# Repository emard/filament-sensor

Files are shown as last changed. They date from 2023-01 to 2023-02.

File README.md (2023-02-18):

# Filament Sensor

Sensor detects presence or absence of the filament.
Openscad 3D Printable models for filament sensors
with cotactless Hall sensor or with mechanical microswitch.

# Hall sensor

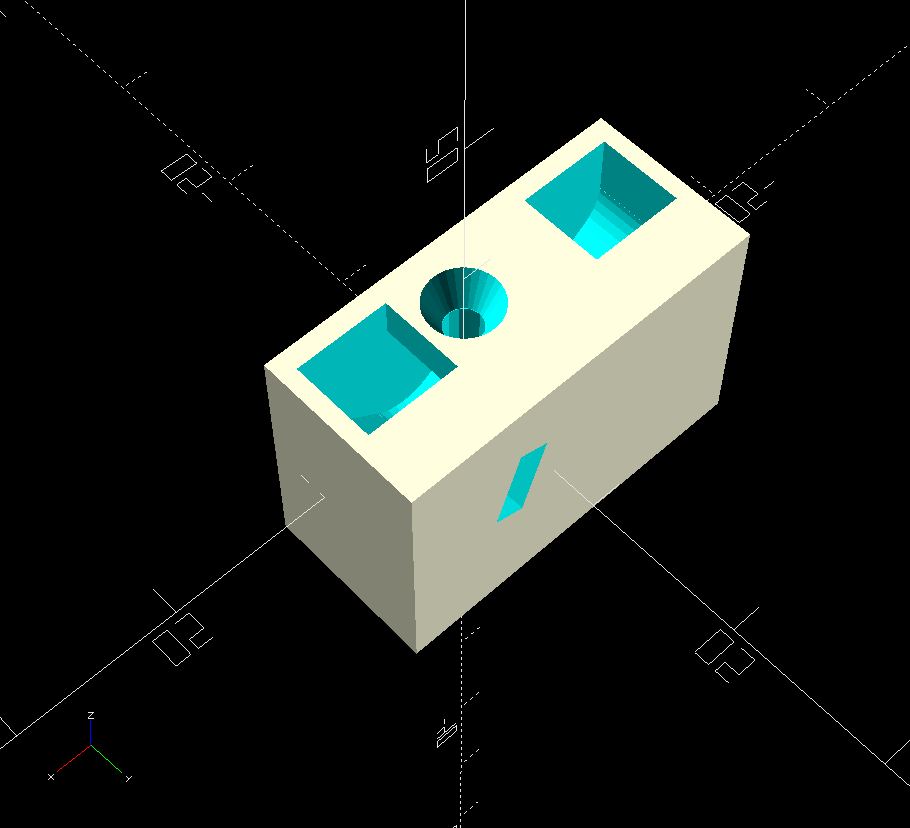
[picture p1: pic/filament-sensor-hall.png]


Applies very small force to the filament,
minimizing friction.

    prusa has this logic in its original IR filament sensor
    sensor OUT:
    0 (LOW)  LOADED
    1 (HIGH) EMPTY
    IR sensor pinout
    +  +5V
    O  OUT
    -  GND
    
    MK2S rambo13a 10-pin connector looking at PCB pins
    ---------
    x x x x x
    x s x - +
    ---------
    -=GND, +=+5V, s=signal
    
    MK3 einsy10a 10-pin connector looking at PCB pins
    ---   ---
    x x x x x
    s x x - +
    ---------
    -=GND, +=+5V, s=signal
    
    HALL sensor Honeywell SS411P or SS495A
    on package is written 411P or 95A
    pinout looking at pins, plastic case at the back
      _______
     / + - o \
     ---------
    
    connect
     - -
     + +
     s o
    
    Prusa MK2.5S firmware can be loaded to MK2S
    Support -> Sensor info
    Fil. sensor: 1-LOADED, 0-EMPTY

Magnet (5x5 mm Neodymium cylinder) is the only moving
part. Solid state Hall sensor (Honeywell SS495A or similar for 5V)
in 3-pin transistor plastic case directly connects to
printer motherboard electronics.

When sensor is empty, magnet is placed at the
position in channel close to the empty filament
guide. Inserted filament displaces the magnet.

Best location for the Hall sensor is where magnetic
flux reverses sign when filament is inserted,
so the sensor reliably reads logical 1 or 0.
To invert logic, flip both magnets or flip the sensor.

Flipping or using different sensor may need adjustment,
experiment with position along the channel, in case of
false runout, reduce the X parameter in steps of 0.1:

    hall_pos = [X,Y,Z];

Hall sensor used is SS411P digital output with bipolar
triggering in range of +50/-50 Gauss or SS495A analog
rail-to-rail output with high sensitivity 3 mV/Gauss = 30 V/Tesla.
AH3377 with unipolar triggering in range of +115/+90
Gauss can be used too but I haven't tried it.

Cut small piece of universal PCB, solder 3-pin connector
on top side, sensor on bottom side. Insulate sensor
middle terminal (-) as it crosses over (o) terminal.
Default sensor orientation is flat side towards filament.

When filament moves thru the guide, it can
either slide over the magnet or rotate the
magnet in the channel. In either case, friction
is very small.

When filament is removed, magnet returns to its
default position by its own weight or by attractive
force from the second magnet.

Second magnet should be used if filament sensor is
not always vertical. It provides a more reliable return
but it increases force, increasing the friction too.
Friction can be tuned by varying distance of
second magnet from the filament detection magnet.

Attractive force holds magnets together so they
won't leave sensor easily. To remove inserted
DxH=5x5 mm magnets, insert filament, try to shake
it out, touch it with some steel or approach
external magnet DxH=10x5 mm from the side and
drag it.

# Mechanical switch

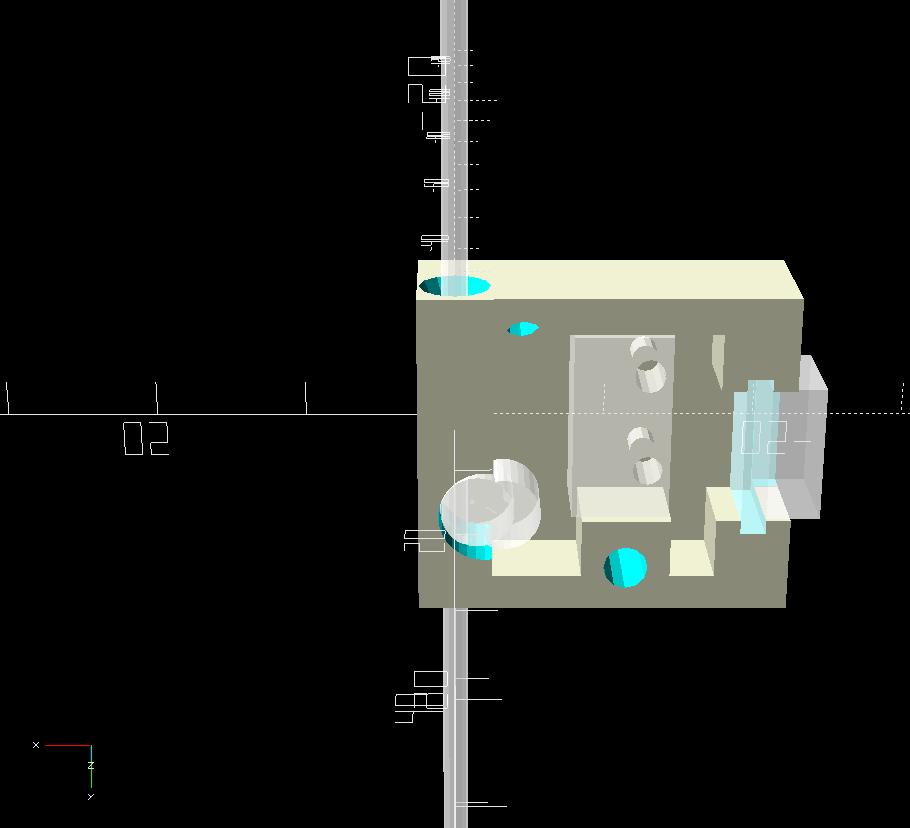
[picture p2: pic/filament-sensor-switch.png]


Applies more friction to the filament than
the Hall sensor.

Mechanical switch with roller applies its designed
force to the filament. Roller should be precisely
positioned relative to the filament to reliably
trigger so there is not much space to tune the
force.

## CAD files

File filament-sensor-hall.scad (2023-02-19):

// filament sensor with magnet and HALL sensor

// prusa has this logic in its original IR filament sensor
// sensor OUT:
// 0 (LOW)  LOADED
// 1 (HIGH) EMPTY
// IR sensor pinout
// +  +5V
// O  OUT
// -  GND

// MK2S rambo13a 10-pin connector looking at PCB pins
// ---------
// x x x x x
// x s x - +
// ---------
//    P3
// -=GND, +=+5V, s=signal

// MK3 einsy10a 10-pin connector looking at PCB pins
// ---   ---
// x x x x x
// s x x - +
// ---------
// -=GND, +=+5V, s=signal

// HALL sensor Honeywell SS495A, on package is written 95A
// pinout looking at pins, plastic case at the back
//   _______
//  / + - o \
//  ---------

// connect
//  - -
//  + +
//  s o

// Prusa MK2.5S firmware can be loaded to MK2S
// Support -> Sensor info
// Fil. sensor: 1-LOADED, 0-EMPTY

hall_pos = [0.0,0,6]; // in case of false filament runout, decrease X in steps of 0.1

hall_sensor_dim = [5,5,1.8];
//hall_sensor_dim = [4.06, 3.0, 1.6]; // Honeywell SS495A package, with enlarge factor for hole
filament_hole_d = 2.3; // 1.75mm should freely passthru

// the filament sensor cube dim
guide_dim=[25,16,8+3]; // reduce Z to see cross-section
guide_pos=[-2.5,0,1.5];

magnet2_pos = [-5,0,0]; // adjust X to tune force

connector_pcb_cube=[1.7,13,7.7];
connector_pcb_pos=[-12,0,9];


mounting_holes=[[-3,-5],[6,5],[-6,5]];

module hall_sensor()
{
  cube(hall_sensor_dim, center=true);
}

module magnet()
{
  cylinder(d=magnet_dim[0], h=magnet_dim[1], $fn=24, center=true);
}


module filament()
{
  translate([0,0,0])
    rotate([90,0,0])
    cylinder(d=1.75,h=70,$fn=12,center=true);
}

module roller_cutter(have_sensor=1)
{
  roller_pos = [2.0,-1,0];
  roller_dim = [6.0,5.4]; // DxH
  channel_angle = 38; // fall down angle
  channel_dim = [5,roller_dim[0],roller_dim[1]]; // from center of roller, at fall down angle
  top_insert_dim = [10,roller_dim[0]+0,roller_dim[1]];
  // roller cut
  translate(roller_pos)
  cylinder(d=roller_dim[0],h=roller_dim[1],$fn=32,center=true);
  // angular
  translate(roller_pos)
  rotate([0,0,-channel_angle])
  {
    // channel
    translate([channel_dim[0]/2,0,0])
    cube(channel_dim,center=true);
    // circular knee transition to upwards channel
    translate([channel_dim[0],0,0])
      cylinder(d=top_insert_dim[1],h=roller_dim[1],$fn=32,center=true);
    // cut upwards channel to insert magnet
    translate([channel_dim[0],0,0])
    rotate([0,0,-90+channel_angle])
    translate([top_insert_dim[0]/2,0,0])
    cube(top_insert_dim,center=true);
    // cut for sensor
    if(have_sensor>0.5)
    translate(hall_pos)
      //rotate([0,0,channel_angle])
      rotate([90,0,90+channel_angle/4])
      cube(hall_sensor_dim,center=true);
  }
}


module filament_guide()
{
  difference()
  {
    union()
    {
      // guide block
      translate(guide_pos)
        cube(guide_dim,center=true);
    }
    // main roller hole and sensor
    roller_cutter();
    // additional magnet to increase force
    translate(magnet2_pos) // more X distance less force
      scale([-1,1,1]) // mirror
        roller_cutter(have_sensor=0);
    // filament hole thru all
    rotate([90,0,0])
    {
      cylinder(d=filament_hole_d,h=50,$fn=12,center=true);
      // overhang fix
      if(0)
      translate([0.4,0,0])
        cylinder(d=filament_hole_d*0.8,h=50,$fn=12,center=true);
      // conical lead-in
      translate([0,0,-guide_pos[1]+2+guide_dim[1]/2-11+8])
        cylinder(d1=filament_hole_d,d2=filament_hole_d*2,h=2.1,$fn=30,center=true);
      // conical lead-out
      if(1)
      translate([0,0,-guide_pos[1]+2-guide_dim[1]/2+11-12])
        cylinder(d2=filament_hole_d,d1=filament_hole_d*2.08,h=2.1,$fn=30,center=true);
    }
  }
}

module holder_bars()
{
  // filament entry side
  holder_pos = guide_pos + [0,0,9];
  holder_dim = guide_dim - [0,0,4];
  holder_thick = 2;
  holder_backplate_thick = 1;
  translate(holder_pos)
    difference()
    {
      cube(holder_dim,center=true);
      translate([0,0,-holder_backplate_thick/2-0.01])
      cube(holder_dim+[-holder_thick*2,-holder_thick*3,-holder_backplate_thick],center=true);
    }
}

module baseplate()
{
    translate([10,2,-1.5-6/2])
      cube([25,22,3],center=true);
}

module screw_holes(d=3, h=30)
{
  // mounting holes
  for(i=[0,1,2])
      translate(mounting_holes[i])
        rotate([0,0,90])
          cylinder(d=d,h=h,$fn=12,center=true);
}

module connector_pcb()
{
  translate(connector_pcb_pos)
  cube(connector_pcb_cube,center=true);
  // connector front cut
  translate(connector_pcb_pos+[-2,0,0])
    cube([5,10,7],center=true);
}

// mounting spacer with connector cut and screw holes
module spacer()
{
   difference()
   {
     union()
     {
       holder_bars();
       translate([0,0,10.5])
       screw_holes(d=4,h=7);
     }
     screw_holes(d=1.8);
     translate([0,0,0.2])
     connector_pcb();
   }
}

cableorg_holes_pos = [[0,32], [0,22]];
module cableorg_holes(d=1.8)
{
    // holes for cable organizer
    for(i=[0,1])
    translate(cableorg_holes_pos[i])
      rotate([0,0,0])
        cylinder(d=d,h=20,$fn=12,center=true);
}

module magnets_cover()
{
  standoff = 0.3; // tolerance standoff
  // covers 1st magnet
  translate([-6,-9-standoff,7])
    cube([7,2,7+11],center=true);
  // sovers 2nd magnet
  translate([11,-9-standoff,7])
    cube([7,2,7+11],center=true);
  // connects holders together
  if(0)
  translate([4,-9-standoff,3])
    cube([20,2,10],center=true);
  // standoff "glue"
  translate([2.5,-8-standoff/2,1.5])
    cube([25,standoff,7],center=true);
}

module pendulum()
{
  // for M8 rod
  pendulum_dim = [7,40,7];
  pendulum_pos = [0,28,1.5];
  ring_inner_d =  9;
  ring_outer_d = 15;

  // for printed holder old design
  /*
  pendulum_dim = [7,40,5];
  pendulum_pos = [0,28,0.5];
  ring_inner_d = 10;
  ring_outer_d = 15;
  */

  difference()
  {
    union()
    {
      translate(pendulum_pos)
        cube(pendulum_dim, center=true);
      translate(pendulum_pos+[0,pendulum_dim[1]/2,0])
        cylinder(d=ring_outer_d,h=pendulum_dim[2],$fn=32,center=true);
    }
    // hole for bearing
    translate(pendulum_pos+[0,pendulum_dim[1]/2,0])
        cylinder(d=ring_inner_d,h=pendulum_dim[2]+1,$fn=32,center=true);
    cableorg_holes();
  }
  magnets_cover();
}

module cable_cover()
{
  difference()
  {
    translate([0,27,5])
    cube([7,15,3],center=true);
    translate([0,27,4])
    cube([8,6,1.01],center=true);
    cableorg_holes(d=3);
  }
}

module pendulum_holder_screw_holes()
{
  mounting_holes=[[10,10,0],[-10,-10,0]];
     // mounting holes
  for(i=[0,1])
      translate(mounting_holes[i])
        rotate([0,0,90])
        {
          cylinder(d=1.8,h=20,$fn=12,center=true);
          // hole for sunken head
          if(0)
          translate([0,0,5])
          cylinder(d=6,h=10,$fn=12,center=true);
        }
}

module pendulum_holder()
{
  plate_box = [25,30,4];
  axis_pos = [0,-3,0];
  axis = [8,6]; // d,h
  difference()
  {
    cube(plate_box,center=true);
    pendulum_holder_screw_holes();
  }
  // axis
  translate(axis_pos+[0,0,plate_box[2]/2+axis[1]/2])
  difference()
  {
    cylinder(d=axis[0],h=axis[1],$fn=32,center=true);
    // screw hole
    cylinder(d=1.8,h=axis[1]+1,$fn=32,center=true);
  }
  // filament holder
  if(1)
  translate([0,12,7])
    cube([5,6,10],center=true);
  // circular holder
  translate([0,12,30])
    rotate([90,90,0])
    difference()
    {
      cylinder(d=40,h=6,$fn=6,center=true);
      cylinder(d=30,h=11,$fn=6,center=true);
    }
}

module holder_disc()
{
  difference()
  {
    cylinder(d=15,h=2,$fn=32,center=true);
    cylinder(d=3,h=3,$fn=32,center=true);
  }
}

module pendulum_assembly()
{
  translate([0,0,12])
  rotate([180,0,180])
  spacer();
  pendulum();  
}

// sensor
module sensor_assembly()
{
rotate([-90,0,0])
{
%filament();
%connector_pcb();
difference()
{
  union()
  {
    filament_guide();
    //holder_bars();
  }
  connector_pcb();
  screw_holes();
}
translate([0,0,12+1])
rotate([180,0,180])
%pendulum_assembly();
// %spacer();
}
}

if(1)
  sensor_assembly();

// pendulum with backplate
if(0)
{
  pendulum_assembly();
}

// pendulum holder to be screwd on snap-on adapter
if(0)
{
  pendulum_holder();
}

// disc on top of the holder
if(0)
  holder_disc();

// spacer disk for too long screws
if(0)
  difference()
  {
    cylinder(d=6.0,h=1.5,$fn=12,center=true);
    cylinder(d=2.5,h=2.0,$fn=12,center=true);
  }

if(0)
  cable_cover();

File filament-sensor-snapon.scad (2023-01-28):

frame_cube=[40.4,6.4,50];


snapon_points=[
 // bottom part near frame
 [-frame_cube[0]/2,frame_cube[1]/2],[-frame_cube[0]/2,-frame_cube[1]/2],
 // click notch slightly up
 [-frame_cube[0]/2+1,-frame_cube[1]/2],[-frame_cube[0]/2,-frame_cube[1]/2-2],
 // bottom edge
 [-25,-frame_cube[1]/2-2],[-25,9],
 // back side
 [25,9],[25,-9],
 // holder notch
 [15,-9],[15,-frame_cube[1]/2],[frame_cube[0]/2,-frame_cube[1]/2],
 // angled insertion helper
 [frame_cube[0]/2,frame_cube[1]/2+1],[15,frame_cube[1]/2]
 // insertion
];

extbar_thick = 5.5;
angular_adjust = 3;
extbar_points = [
  // go up
  [25,-9], [30,-9],
  // lean forward
  [70,-60], [160, -60],
  // back side return
  [160, -60+extbar_thick], [70+angular_adjust, -60+extbar_thick],
  // return down
  [30+angular_adjust,-9+extbar_thick], [25,-9+extbar_thick]
];

module frame()
{
  cube(frame_cube,center=true);
}

module mounting_holes_cutter()
{
  // [[4.5,-6],[11.5,10]];
  offset=[145,-60,0];
  holes_pos=[[offset[0]+10,offset[1],offset[2]-10],[offset[0]-10,offset[1],offset[2]+10]];
  for(i=[0,1])
    translate(holes_pos[i])
      rotate([90,0,0])
      cylinder(d=3,h=20,$fn=12,center=true);
}

module snapon_clip()
{
  linear_extrude(30,center=true)
  polygon(points=snapon_points);
}

module snapon_clip_with_holes()
{
  difference()
  {
    union()
    {
      snapon_clip();
      extension_bar();
    }
    mounting_holes_cutter();
  }
}

module extension_bar()
{
  linear_extrude(30,center=true)
  polygon(points=extbar_points);
}

%frame();
snapon_clip_with_holes();

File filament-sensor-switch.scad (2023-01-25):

// switch D2F-01L2-D with big roller 5mm dia
// https://omronfs.omron.com/en_US/ecb/products/pdf/en-d2f.pdf

// prusa this logic in its original IR filament sensor
// sensor OUT:
// 0 (LOW)  filament inserted
// 1 (HIGH) filament runout

// MK2S 10-pin connector looking at PCB pins
// ---------
// x x x x x
// - s x - +
// ---------
// -=GND, +=+5V, s=signal

// MK3 10-pin connector looking at PCB pins, notch on top
// ---   ---
// x x x x x
// s x x - +
// ---------
// -=GND, +=+5V, s=signal

// switch pinout, button on top left
//  _-___
// |_____|
//  N O C
//
//  N-O : NO (normally open)
//  N-C : NC (normally closed)

// connect bare switch
// - O
// + C
// s N

adjust_click = 0.2; // to reliably click move +:closer -:away from filament
filament_hole_d = 2.4; // 1.75mm should freely passthru

module switch()
{
  swbox = [6.5,12.7,5.7];
  hole_pos = [[5,3],[5,-3.5],[5,-3.8]];
  hole_dia = 2;
  roller = [5,4]; // dxh
  roller_pos = [[-6.3,12.7/2,0],[-4.5,12.7/2+0.2,0]];
  // body
  difference()
  {
    translate([swbox[0]/2,0,0])
      cube(swbox, center=true);
    // holes
    for(i=[0,1,2])
    {
      translate(hole_pos[i])
        cylinder(d=hole_dia,h=swbox[2]+1,$fn=12,center=true);
    }
  }
  // roller
  for(i=[0,1])
    translate(roller_pos[i])
      cylinder(d=roller[0],h=roller[1],$fn=32,center=true);
}

module filament()
{
  translate([0,0,0])
    rotate([90,0,0])
    cylinder(d=1.75,h=70,$fn=12,center=true);
}

module filament_guide()
{
  difference()
  {
    union()
    {
      // guide block
      translate([0,2,0])
        cube([5,22,6],center=  true);
    }
    // roller cut
    translate([2,6.25,0])
    cylinder(d=6.3,h=10,$fn=32,center=true);
    // filament hole thru all
    rotate([90,0,0])
    {
      cylinder(d=filament_hole_d,h=50,$fn=12,center=true);
      // overhang fix
      translate([0,0.4,0])
        cylinder(d=filament_hole_d*0.8,h=50,$fn=12,center=true);
      // conical lead-in
      translate([0,0,8])
        cylinder(d1=filament_hole_d,d2=filament_hole_d*2,h=2.1,$fn=12,center=true);
      // conical lead-out
      if(1)
      translate([0,0,-12])
        cylinder(d2=filament_hole_d,d1=filament_hole_d*2,h=2.1,$fn=12,center=true);
    }
  }
}

module holder_sticks()
{
  sticks_h=2;
  sticks_pos=[[-8.5+13.5,3,-2],[-8.5+13.5,-3.6,-2]];
  for(i=[0,1])
    translate(sticks_pos[i])
      rotate([0,0,0])
        cylinder(d=1.8,h=sticks_h,$fn=12,center=true);
}

module holder_bars()
{
  // filament entry side
  translate([4+11.5-3,-7.8,0])
    cube([20,2.4,6],center=true);
  // filament exit side
  translate([4+11.5-3,11.8,0])
    cube([20,2.4,6],center=true);
  // switch side near roller
  translate([11.5,9.8,0])
    cube([6,6.4,6],center=true);
  // holds pcb filament entry side
  translate([20,-4.6,0])
    cube([5,4,6],center=true);
  // holds pcb filament exit side
  translate([20,8.6,0])
    cube([5,4,6],center=true);
}

module baseplate()
{
    translate([10,2,-1.5-6/2])
      cube([25,22,3],center=true);
}

module screw_holes()
{
  mounting_holes=[[4.5,-6],[11.5,10]];
     // mounting holes
  for(i=[0,1])
      translate(mounting_holes[i])
        rotate([0,0,90])
          cylinder(d=3,h=20,$fn=12,center=true);
}

connector_pcb_cube=[1.7,11,7.7];
connector_pcb_pos=[20,2.05,-0.84];

module connector_pcb(scl=[1,1,1])
{
  translate(connector_pcb_pos)
  scale(scl)
  cube(connector_pcb_cube,center=true);
  // connector front cut
  translate(connector_pcb_pos+[2,-0.1,0])
    cube([5,9.2,7],center=true);
}


scale([-1,1,1]) // mirror X-direction, cable on the left
{
switch_pos=[8-adjust_click,0,0]; // adjust X to reliably clock with filament inserted
translate(switch_pos)
  %switch();
%filament();
%connector_pcb();
filament_guide();
translate(switch_pos)
  holder_sticks();
difference()
{
  union()
  {
    filament_guide();
    baseplate();
    holder_bars();
  }
  screw_holes();
  connector_pcb();
}
}

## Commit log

2023-01-25 switch picture
2023-01-25 connector cut
    [filament-sensor-hall.scad]
2023-01-25 adjusting dims, moving sensor 0.2 mm bit away from filament to to better adjust triggering point
    [filament-sensor-hall.scad]
2023-01-25 readme sensor orientation
2023-01-25 adjust sensor pos for triggering
    [filament-sensor-hall.scad]
2023-01-25 cleanup and adjusting dims to fit connector
    [filament-sensor-hall.scad]
2023-01-25 magnets more separaterd - adjusting dims to reliably trigger
    [filament-sensor-hall.scad]
2023-01-25 readme removing magnets
2023-01-26 adjusting dims, pendulum arm and holder
    [filament-sensor-hall.scad]
2023-01-26 prusa snap-on adapter
    [filament-sensor-snapon.scad]
2023-01-26 fine adjust for false runout
    [filament-sensor-hall.scad]
2023-01-26 holder to snapon screws from the back
    [filament-sensor-hall.scad, filament-sensor-snapon.scad]
2023-01-27 pandulum thicker and with cable org
    [filament-sensor-hall.scad]
2023-01-27 hexagonal holder
    [filament-sensor-hall.scad]
2023-01-28 spacer disc for long screws
    [filament-sensor-hall.scad]
2023-01-28 sensor info
2023-01-28 adjust sensor position to reduce false runout
    [filament-sensor-hall.scad]
2023-01-28 sensors described
2023-01-28 removing magnets
2023-01-28 snapon thicker
    [filament-sensor-snapon.scad]
2023-01-29 typo in pinout
    [filament-sensor-hall.scad]
2023-02-17 P3 connector name
    [filament-sensor-hall.scad]
2023-02-18 commented pendulum for M8 rod (need unification with existing holder)
    [filament-sensor-hall.scad]
2023-02-18 readme for digital output sensor SS411P
2023-02-18 pendulum improve holder bars
    [filament-sensor-hall.scad]
2023-02-18 readme sensor PCB
2023-02-18 adjust sensor pos for SS411P (reduce chance of false runout)
    [filament-sensor-hall.scad]
2023-02-19 magnets cover to prevent jump-out at filament insertion
    [filament-sensor-hall.scad]
